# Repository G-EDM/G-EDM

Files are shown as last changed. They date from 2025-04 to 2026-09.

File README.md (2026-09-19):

</br>
</br>
</br>

```diff
 ______     _______ ______  _______
|  ____ ___ |______ |     \ |  |  |
|_____|     |______ |_____/ |  |  |      

Overview / Gateway
```                                                               

</br>
</br>

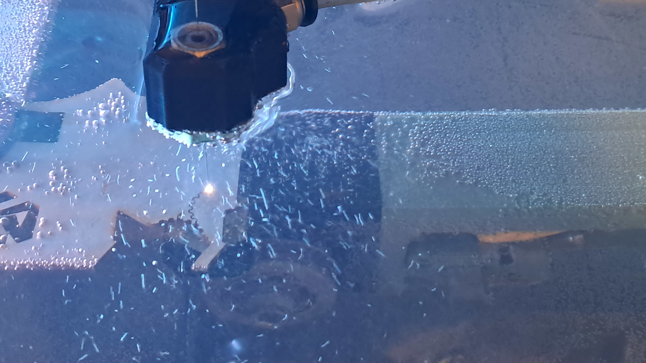
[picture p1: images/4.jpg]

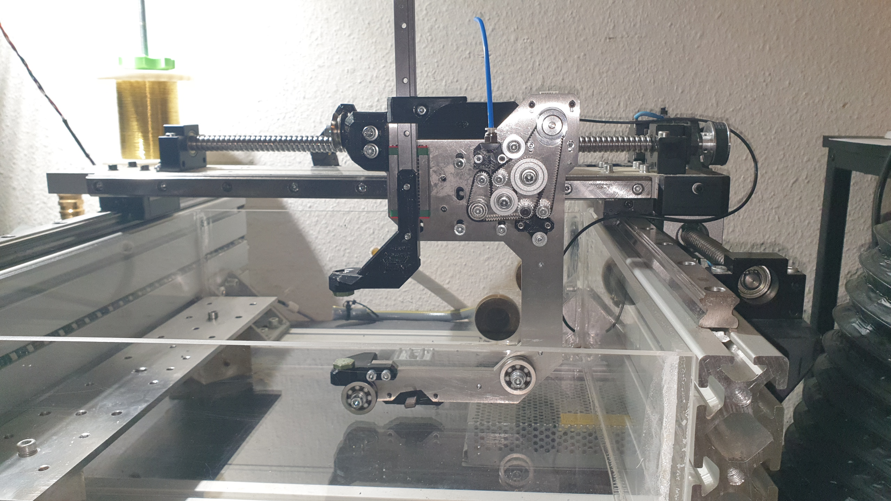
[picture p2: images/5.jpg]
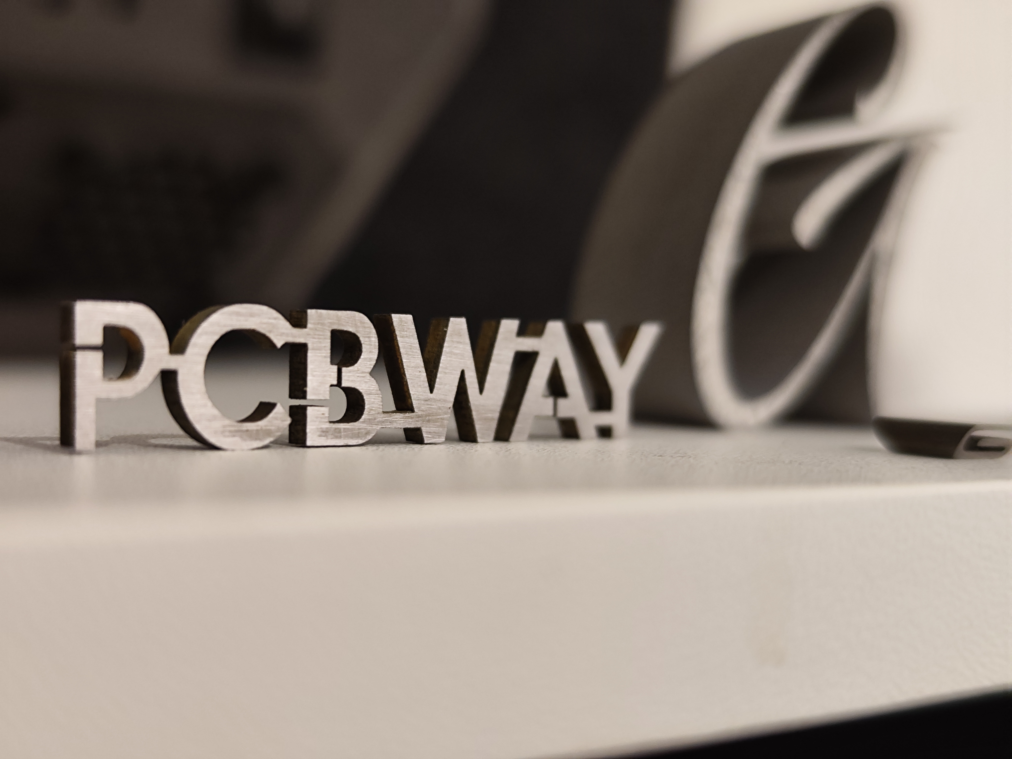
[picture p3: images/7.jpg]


</br>
</br>

# About the project

G-EDM provides Hard- and Software solution for DIY sinker and wire EDM machining targeting the hobby market while trying to keep the project affordable and low budget compatible. While this is one of the main goals there are no compromises made in regards of precision and machine rigidity.

The project evolved over time and so did the mechanical design, the electronics and the firmware.

This repo acts as a gateway to all the other repos and is a way to start the journey into the world of DIY electrical discharge machining.

There are currently two different core version of the electronics and firmware in circulation. The EVOII/III are the initial releases. The new Gapstorm components are the current and upcoming versions. 

Since the sensing circuitry has slightly changed the Gapstorm firmware is not compatible with the EVO pulseboard.

It is possible to upgrade the EVOII and III Pulseboard to match the Gapstorms. A tutorial on how to do that will follow soon. After that upgrade those baords can be used with the new firmware.

</br></br>

# Mechanics

The repo for the new gapstorm router is available here:

[Gapstorm router](https://github.com/G-EDM/gedm-gapstorm/tree/main)

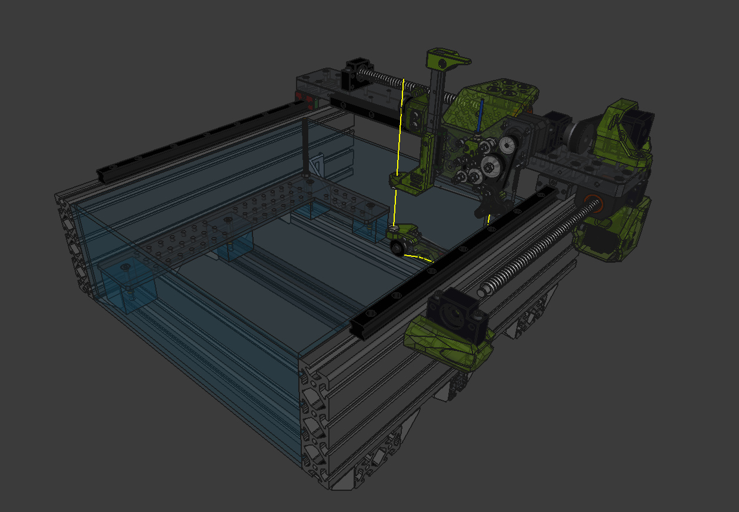
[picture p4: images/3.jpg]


</br></br>

# Electronics

The BOM for the control unit is included on this repo:

[BOM for the control unit](./control-unit-BOM.md)

Files for the PCBs are available on PCBway. To build the electronics it requires two custom PCBs. The switching PCB and the Controlboard aka Motionboard. 

The current PCBs are the Gapstorm Pulseboard and the EVOIII Motionboard.

[Gapstorm Pro Pulseboard on PCBway](https://www.pcbway.com/project/shareproject/G_EDM_Gapstorm_Pro_Pulseboard_a0db8e30.html)

[EVOIII Motionboard on PCBway](https://www.pcbway.com/project/shareproject/W532897ASC41_motionboard_evoIII_rev3_bb113e0f.html)

</br>
Tip: The Motionboard should be mounted outside of the control box that includes the Pulseboard. One way is shown on the image below using the 3D printed EVOIII Panel.
</br></br>
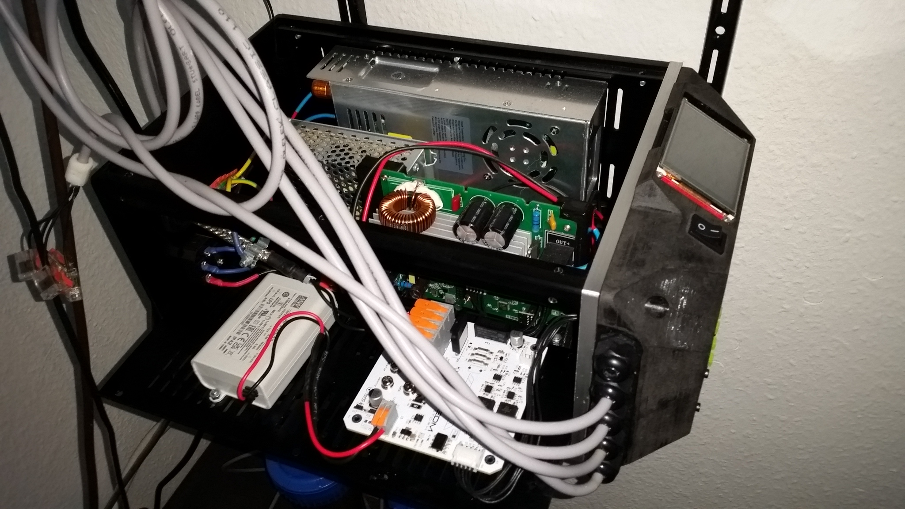
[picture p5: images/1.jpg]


More images are available here:

[Gapstorm Image gallery](https://gedm.org/photos/1/album/a655d21b876f5ba21783beb6c846ac8f)

</br></br>

# 3D printed control panel

Designed to fit a 2.8" display (see the BOM)

[EVOIII Control panel](https://github.com/G-EDM/G-EDM-EVOIII-Controlpanel)

</br></br>

# Firmware

The Repo for the Gapstorm firmware:

[Gapstorm G-RBL](https://github.com/G-EDM/G-RBLv3)

The Repo for the EVOII and EVOIII Pulseboard firmware (deprecated and not compatible with the gapstorm Pulseboard)

[EVOII/III G-RBL](https://github.com/G-EDM/G-RBL-experimental)

</br></br>

# Spool holder for P5 spools

[P5 Spool holder](https://github.com/G-EDM/spool-controller)

</br></br>

# Wiki

There is no real wiki but I posted some of the most important things on the homepage that will act like some kind of a wiki:

[G-EDM FAQ and Wiki](https://gedm.org/user/1)

</br></br>

# Contact

gedm-support@proton.me

[Join the project on Discord](https://discord.gg/vWSmpkzVrj)

[G-EDM Website](https://gedm.org)

</br>
</br>

# Donations

Bitcoin: bc1qkz8vwrd3pupewdtyg09qj9nv249vlgdy4ffhyv

Paypal: https://www.paypal.com/donate/?hosted_button_id=QP5LHGRUCXXBL

</br>   
</br>

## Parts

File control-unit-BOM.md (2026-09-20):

1x G-EDM Pulseboard

1x G-EDM Motionboard

1x ESP32 WROOM32 AZdelivery 38Pins CP2102

1x ILI9341 SPI SD TOUCH

4x TMC2209 v2 with big heatsink

1x rocker switch (ON/OFF)

JST wires of different types.

1x 12V Cooling fan (No high speed fans. Simple 120mmx20mm silent fan is ok. High Speed fans may induce noise etc.)

1x MEAN WELL APV-35-12 36W 12V 3A PSU

1x 12v 10A PSU

1x Lianshi 6A 0-80V variable voltage PSU

ONE of those (TTL version! NOT RS-485 and also not the RF version!):

    1x DPH8909 Programmable Power Supply TTL 0-96V 0-9.6A

    1x DPM8605 Programmable Power Supply TTL 0-60V 0-5A

# Cutting currents

For wire EDM current from 0.4A to 1.6A are ok to use. Depends on how good the wire feeder is and how thick the wire.
I normally settle at 1.2A or something like that. 

# Warning

EDM creates a lot of EMI noise. The motionboard with the sensitive ESP and SPI communication needs to be isolated from the 
pulsing engine. And it also should not be placed next to the sparks. A strong discharge can mess things up pretty easy.

The pulse electronics and all PSUs need to be placed inside a metal box and the motionboard needs to be outside of this box.
Best case would be to put the motionboard into a second metalbox. There are some limits about the distance between motionboard and pulseboard. The wires should be kept as short as possible and the DPH/DPM interface wire can create problems if it is too long.

# Notes

The ON/OFF switch is required! Limit switches are optional. The ON/OFF switch acts as eStop in the process too. If it is not connected or turned to OFF the process will not start and all motion is blocked.

# ESP32 note

Go for the AZdelivery boards. So far everyone who bought a cheap knockoff had issues of some kind. Inverted colors on the display was one of them. It is the heart of everything. Don't cheap out on that.

# ILI9341

There are hundreds of different version available. Not only different sizes but also different communication interface, with or without touch and with or without SD card and also different touch controllers.

The display needs to use SPI communication, XPT touch controller and provide a SD card reader.
2.8" size is nice but 2.4" works too.

It is also recommended to use the AZdelivery display.

# DPM8605 vs DPH8909

The DPH8909 will allow a higher voltage. From what I have seen it is not really needed. Cutting at 80V sounds and looks really
impressive but the surface finish is ugly. 70V is a nice working voltage. So far all showcase cuts where done with the DPM8605
at 60V and only one with the DPH8909.

The DPM8605 is still not deprecated and a valid option. It costs only half of what the DPH costs and is easily available. The DPH8909 in
the TTL version ships from china and can take two weeks to deliver.

DPM8605 has a max input voltage of around 70v. I recommend 65-70v to power it. DPH8909 can take the full max voltage of the 0-80V PSU without problems.

# About the 12V 10A PSU:

I use this exact model from Kingwen:
https://www.amazon.de/dp/B08QCNYLY8

A different one was tested but it induced noise into the motionboard and messed a little with the feedback signal.
If the cFd feedback does not produce a stable 0 reading without load the 12v PSU may be the first thing to check.
The Kingwen never made any troubles.

# About the variable voltage PSU

They don't all produce the exact same max output voltage. Some are very close to 80v and some can go up to 84v.
It is ok to use 84v if the DPH8909 is used but with the DPM8605 it needs to be set to 70v max.

Lianshi 0-80v variable voltage PSU (6A 480W):

https://www.amazon.de/dp/B0BQ33XG33

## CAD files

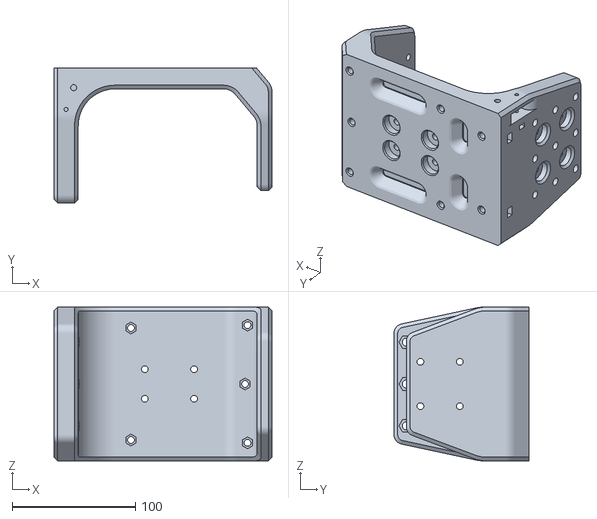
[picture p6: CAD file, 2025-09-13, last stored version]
rev2-x-slide-evoII-backport.stl
177.1 x 109.7 x 125.0

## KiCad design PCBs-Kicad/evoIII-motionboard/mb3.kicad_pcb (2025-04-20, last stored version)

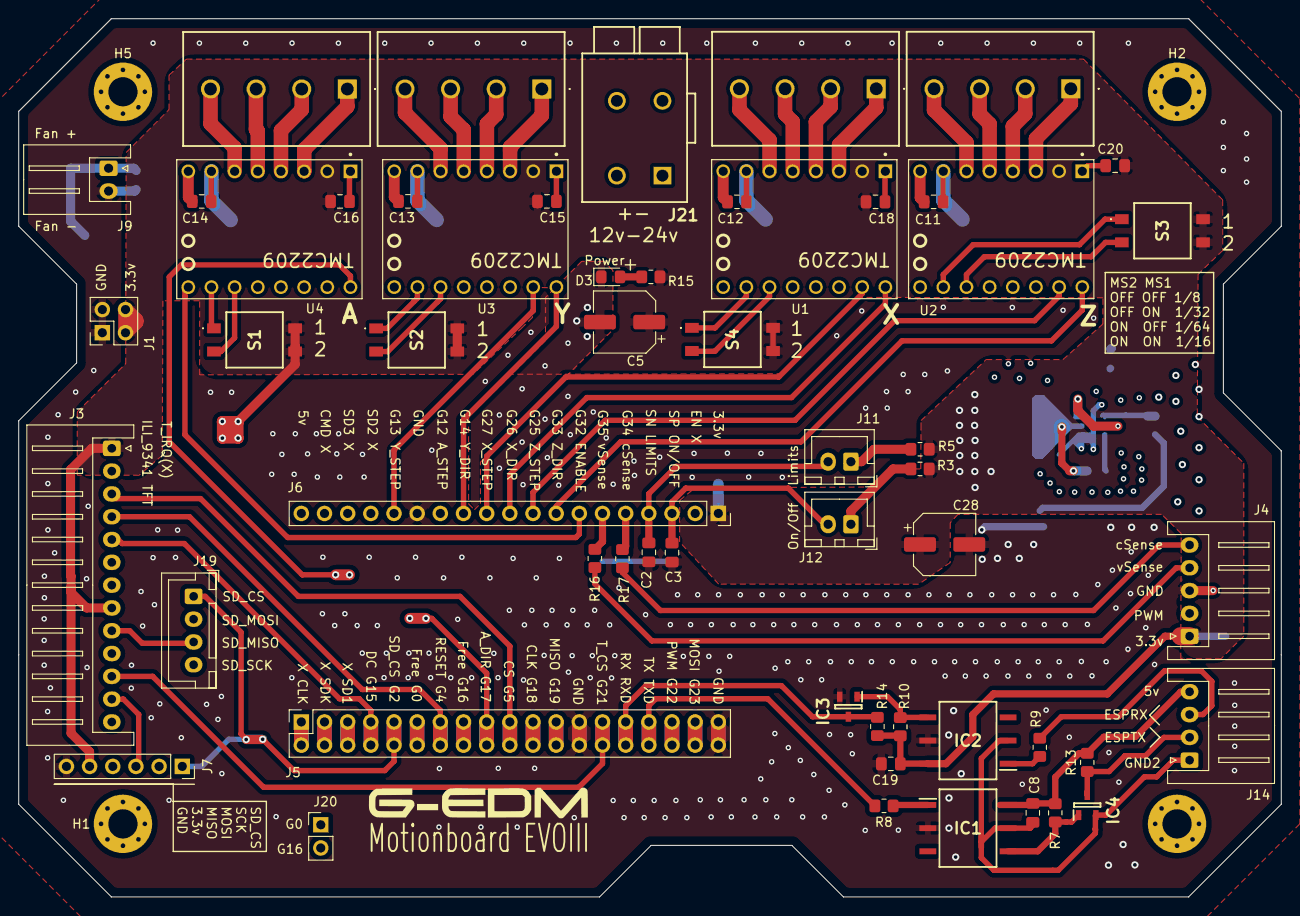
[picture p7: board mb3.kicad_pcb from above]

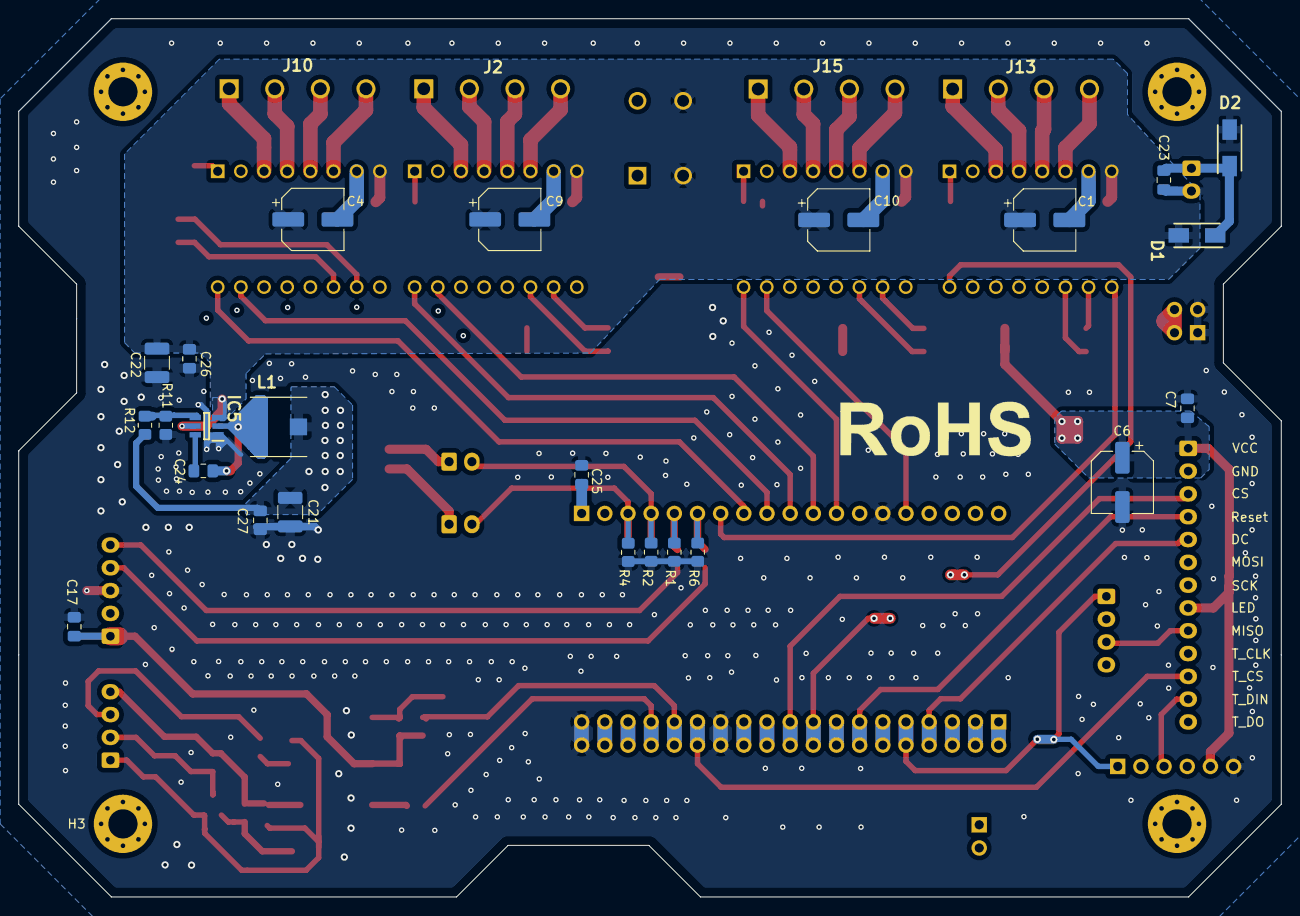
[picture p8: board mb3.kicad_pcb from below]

Board: 4 copper layers, 138.4 x 96.3 mm, 83 parts (24 on the bottom side), 73 nets.

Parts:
C1, C4, C9, C10: EEE-HA1V101XP; CP_Elec_6.3x7.7
C2, C3, C7, C8, C11, C12, C13, C14, C15, C16, C17, C18, C19, C20, C23, C24, C25, C26, C27: 08055C104K4T2A; C_0805_2012Metric_Pad1.18x1.45mm_HandSolder
C5, C6, C28: EEE-HA1C221XP; CP_Elec_6.3x7.7
C21: 22uf-16v-X7R (GRM32ER71C226KEA8K); C_1210_3225Metric_Pad1.33x2.70mm_HandSolder
C22: GRM32ER71H475KA88L; C_1210_3225Metric_Pad1.33x2.70mm_HandSolder
D1, D2: RB168L-60TFTE25; DIOM5026X220N
D3: 597-3305-607F; LED_0805_2012Metric_Pad1.15x1.40mm_HandSolder
H1, H2, H3, H5: MountingHole_Pad; MountingHole_3.2mm_M3_Pad_Via
IC1, IC2: H11L1SR2M; SOT254P916X480-6N
IC3, IC4: MMBT3904; SOT95P240X110-3N
IC5: LMR51420XFDDCR; SOT95P280X110-6N
J1: Conn_02x02_Odd_Even; PinHeader_2x02_P2.54mm_Vertical
J2, J10, J13, J15: 796689-4; 7966894
J3: B13B-XH-A(LF)(SN; JST_XH_S13B-XH-A_1x13_P2.50mm_Horizontal
J4: Conn_01x05_Socket; JST_XH_S5B-XH-A_1x05_P2.50mm_Horizontal
J5: PM254-2-19-Z-8.5; PinSocket_2x19_P2.54mm_Vertical
J6: PM254-1-19-Z-8.5; PinSocket_1x19_P2.54mm_Vertical
J7: Conn_01x06_Socket; PinSocket_1x06_P2.54mm_Vertical
J9: B2B-XH-A(LF)(SN); JST_XH_S2B-XH-A_1x02_P2.50mm_Horizontal
J11, J12: B2B-XH-A(LF)(SN); JST_XH_B2B-XH-A_1x02_P2.50mm_Vertical
J14: B4B-XH-A(LF)(SN); JST_XH_S4B-XH-A_1x04_P2.50mm_Horizontal
J19: B4B-XH-A(LF)(SN); JST_XH_B4B-XH-A_1x04_P2.50mm_Vertical
J20: DNP; PinHeader_1x02_P2.54mm_Vertical
J21: 2604-1102; 26041102
L1: 7447786008; WE-PD_6033_6050_PLASTIC_BASE54
R1, R2, R4, R6, R12, R16, R17: 560112120013; R_0805_2012Metric_Pad1.20x1.40mm_HandSolder
R3, R5: ERJ-T06J102V; R_0805_2012Metric_Pad1.20x1.40mm_HandSolder
R7, R10, R14: RCC0805470RFKEA; R_0805_2012Metric_Pad1.20x1.40mm_HandSolder
R8, R13: RCC0805330RFKEA; R_0805_2012Metric_Pad1.20x1.40mm_HandSolder
R9: MR08X4990FTL; R_0805_2012Metric_Pad1.20x1.40mm_HandSolder
R11: 560112120026; R_0805_2012Metric_Pad1.20x1.40mm_HandSolder
R15: ERJ-T06J221V; R_0805_2012Metric_Pad1.20x1.40mm_HandSolder
S1, S2, S3, S4: 2454985-2; 24549852
U1, U2, U3, U4: TMC2209; MODULE_TMC2209_SILENTSTEPSTICK

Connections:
3.3v+: C5.1, C6.1, C7.1, C15.1, C16.1, C17.1, C18.1, C19.2, C20.1, C21.2, C25.1, C27.2, C28.1, IC2.6 (VCC), J1.3, J1.4, J3.1, J3.8, J4.1, J6.1, J7.5, L1.2, R3.2, R5.2, R10.1, R12.1, R14.2, R15.1, S1.B1 (3), S1.B2 (4), S2.B1 (3), S2.B2 (4), S3.B1 (3), S3.B2 (4), S4.B1 (3), S4.B2 (4), U1.2 (VIO), U2.2 (VIO), U3.2 (VIO), U4.2 (VIO)
12v+: C1.1, C4.1, C9.1, C10.1, C11.1, C12.1, C13.1, C14.1, C22.2, C26.2, D1.2 (A), IC5.3 (VIN), IC5.5 (EN), J21.3 (2.1), J21.4 (2.2), U1.8 (VM), U2.8 (VM), U3.8 (VM), U4.8 (VM)
CLK: J3.7, J3.10, J5.21, J5.22, J7.2, J19.4
CS: J3.3, J5.19, J5.20
DC: J3.5, J5.7, J5.8
DPMRXB: IC4.3 (COLLECTOR), J14.2, R13.1
DPMTXB: J14.3, R9.1
GND: C1.2, C2.2, C3.2, C4.2, C5.2, C6.2, C7.2, C9.2, C10.2, C11.2, C12.2, C13.2, C14.2, C15.2, C16.2, C17.2, C18.2, C19.1, C20.2, C21.1, C22.1, C23.2, C25.2, C26.1, C27.1, C28.2, D2.2 (A), D3.1 (K), IC1.2 (CATHODE), IC2.5 (GND), IC3.2 (EMITTER), IC5.1 (GND), J1.1, J1.2, J3.2, J4.3, J5.25, J5.26, J5.37, J5.38, J6.14, J7.6, J9.2, J21.1 (1.1), J21.2 (1.2), R1.2, R2.2, R4.2, R6.2, R11.2, U1.1 (GND), U1.7 (GND), U2.1 (GND), U2.7 (GND), U3.1 (GND), U3.7 (GND), U4.1 (GND), U4.7 (GND)
GND5v: C8.1, IC1.5 (GND), IC2.2 (CATHODE), IC4.2 (EMITTER), J14.1
GPIO16: J5.15, J5.16, J20.2
Limit39: C2.1, J6.4, J11.2, R2.1
MOSI: J3.6, J3.12, J5.35, J5.36, J7.3, J19.2
Miso: J3.9, J3.13, J5.23, J5.24, J7.4, J19.3
unnamed: C23.1, D1.1 (K), D2.1 (K), J9.1
unnamed: D3.2 (A), R15.2
unnamed: IC1.1 (ANODE), R8.2
unnamed: IC1.4 (VO), IC4.1 (BASE), R7.2
unnamed: IC2.1 (ANODE), R9.2
unnamed: IC2.4 (VO), IC3.1 (BASE), R10.2
unnamed: C24.1, IC5.6 (CB)
unnamed: IC5.4 (FB), R11.1, R12.2
unnamed: C24.2, IC5.2 (SW), L1.1
unnamed: J4.4, R16.1
unnamed: J4.5, R17.1
unnamed: J5.1, J5.2
unnamed: J5.3, J5.4
unnamed: J5.5, J5.6
unnamed: J11.1, R5.1
unnamed: J12.1, R3.1
unnamed: J2.2, U1.4 (M1A)
unnamed: J2.1, U1.3 (M1B)
unnamed: J2.3, U1.5 (M2A)
unnamed: J2.4, U1.6 (M2B)
unnamed: J10.2, U2.4 (M1A)
unnamed: J10.1, U2.3 (M1B)
unnamed: J10.3, U2.5 (M2A)
unnamed: J10.4, U2.6 (M2B)
unnamed: J15.2, U3.4 (M1A)
unnamed: J15.1, U3.3 (M1B)
unnamed: J15.3, U3.5 (M2A)
unnamed: J15.4, U3.6 (M2B)
unnamed: J13.2, U4.4 (M1A)
unnamed: J13.1, U4.3 (M1B)
unnamed: J13.3, U4.5 (M2A)
unnamed: J13.4, U4.6 (M2B)
PWM: J4.2, J5.33, J5.34
RX(IO3): IC3.3 (COLLECTOR), J5.29, J5.30, R14.1
SD_CS: J5.9, J5.10, J7.1, J19.1
Start36: C3.1, J6.3, J12.2, R4.1
TX(IO1): J5.31, J5.32, R8.1
T_CS: J3.11, J5.27, J5.28
VCCB: C8.2, IC1.6 (VCC), J14.4, R7.1, R13.2
adir17: J5.17, J5.18, U4.9 (DIR)
ams1: S1.A1 (1), U4.15 (MS1)
ams2: S1.A2 (2), U4.14 (MS2)
astep12: J6.13, U4.10 (STEP)
enable-all: J6.7, U1.16 (~EN), U2.16 (~EN), U3.16 (~EN), U4.16 (~EN)
gpio0: J5.11, J5.12, J20.1
input35: J6.6, R6.1, R16.2
reset: J3.4, J5.13, J5.14
vSense34: J6.5, R1.1, R17.2
xdir: J6.10, U1.9 (DIR)
xms1: S4.A1 (1), U1.15 (MS1)
xms2: S4.A2 (2), U1.14 (MS2)
xstep: J6.11, U1.10 (STEP)
ydir: J6.12, U3.9 (DIR)
yms1: S2.A1 (1), U3.15 (MS1)
yms2: S2.A2 (2), U3.14 (MS2)
ystep: J6.15, U3.10 (STEP)
zdir: J6.8, U2.9 (DIR)
zms1: S3.A1 (1), U2.15 (MS1)
zms2: S3.A2 (2), U2.14 (MS2)
zstep: J6.9, U2.10 (STEP)

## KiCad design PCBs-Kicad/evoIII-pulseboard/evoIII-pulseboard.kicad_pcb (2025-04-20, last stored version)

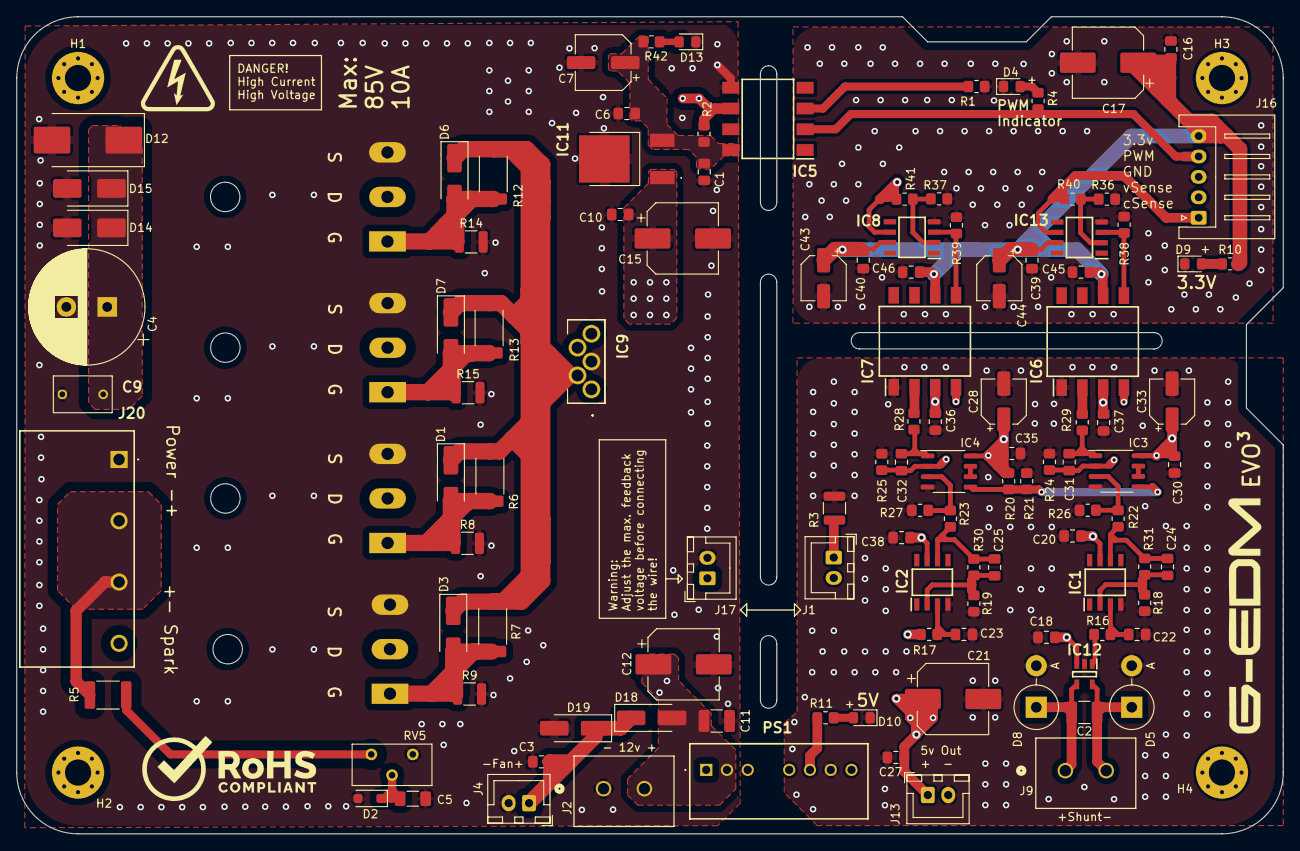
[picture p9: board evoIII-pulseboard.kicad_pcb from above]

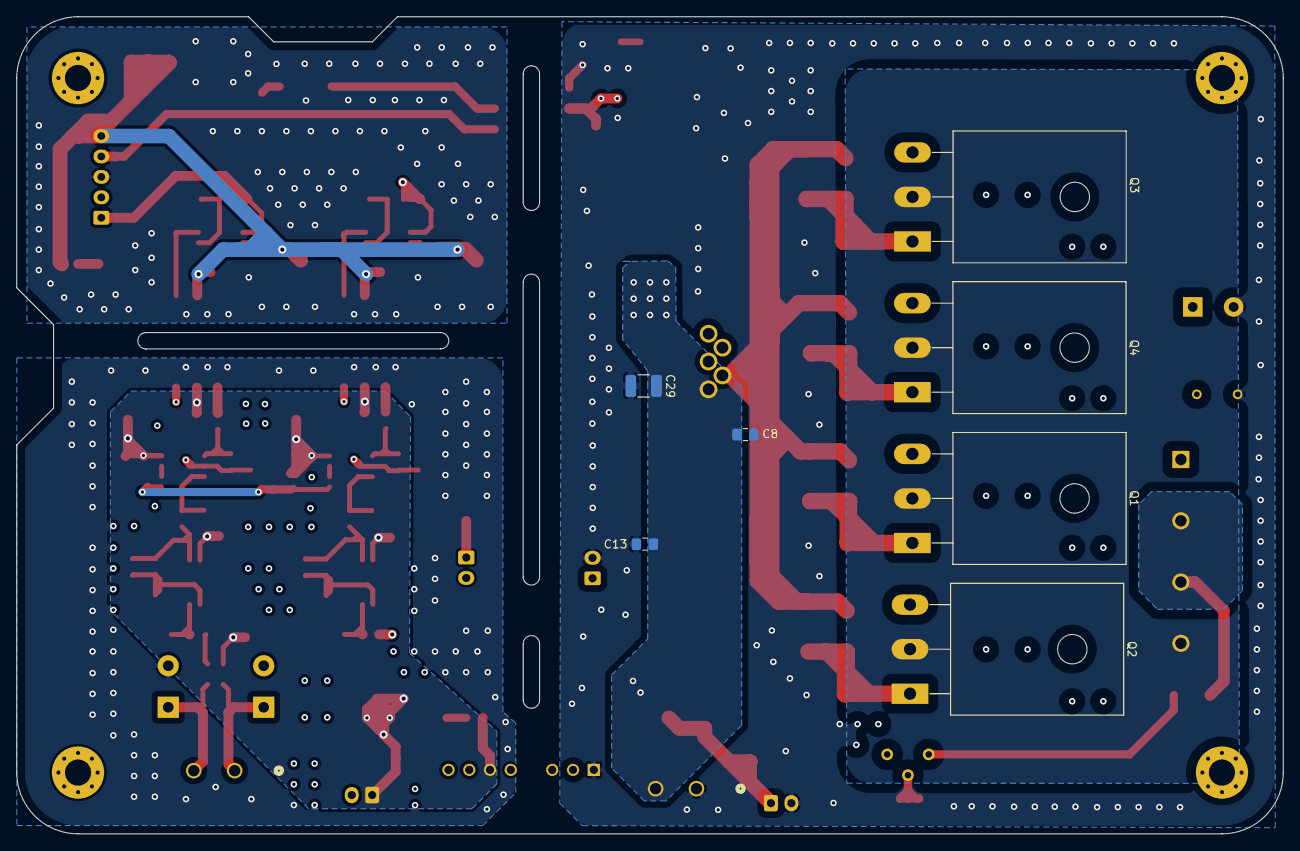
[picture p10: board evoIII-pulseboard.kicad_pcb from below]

Board: 4 copper layers, 155.0 x 100.0 mm, 124 parts (7 on the bottom side), 52 nets.

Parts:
C1, C3, C6, C8, C10, C13, C16, C18, C20, C27, C30, C35, C36, C37, C38, C39, C40, C45, C46: 08055C104K4T2A; C_0805_2012Metric_Pad1.18x1.45mm_HandSolder
C2: 12107A101JAT2A; C_1210_3225Metric_Pad1.33x2.70mm_HandSolder
C4: DNP; CP_Radial_D14.0mm_P5.00mm
C5: DNP; C_1206_3216Metric_Pad1.33x1.80mm_HandSolder
C7: EEE-HAC221XAP; CP_Elec_6.3x7.7
C9: FKP2F004701D00JSSD; FKP2G011001D00KI00
C11, C29: GRM32RR71H105KA01K; C_1210_3225Metric_Pad1.33x2.70mm_HandSolder
C12, C15, C17, C21: EEE-HAV221UAP; CP_Elec_8x10.5
C22, C23, C31, C32: C0805C101J5RACTU; C_0805_2012Metric_Pad1.18x1.45mm_HandSolder
C24, C25: DNP; C_0805_2012Metric_Pad1.18x1.45mm_HandSolder
C28, C33, C43, C44: AVS476M16C12T-F; CP_Elec_5x5.4
D1, D3, D6, D7, D18, D19: B360A-E3/61T; D_SMA_Handsoldering
D2: DNP; D_SOD-123F
D4: APT2012LVBC/D; LED_0805_2012Metric_Pad1.15x1.40mm_HandSolder
D5, D8: 1N5378B; D_DO-201_P5.08mm_Vertical_AnodeUp
D9, D10, D13: SM0805UGC; LED_0805_2012Metric_Pad1.15x1.40mm_HandSolder
D12: MB520_R1_00001; D_SMC_Handsoldering
D14, D15: SMBJ5378B-TP; D_SMB_Handsoldering
H1, H2, H4: MountingHole; MountingHole_3.2mm_M3_Pad_Via
H3: MountingHole_Pad; MountingHole_3.2mm_M3_Pad_Via
IC1, IC2, IC8, IC13: OPA350UA; SOIC127P600X175-8N
IC3, IC4: LM358F-GE2; SOP-8_3.9x4.9mm_P1.27mm
IC5: 6N137S; SOP254P1016X460-8N
IC6, IC7: HCNR201-500E; SOP254P1230X400-8N
IC9: IXDI609CI
IC11: MC7805CDTRKG; MJD1221G
IC12: INA293B3; SOT95P280X145-5N
J1, J13, J17: B2B-XH-A(LF)(SN); JST_XH_B2B-XH-A_1x02_P2.50mm_Vertical
J2: 1776138-2 and 796641-2; CONN2_796643-2_TEC
J4: S2B-XH-A(LF)(SN); JST_XH_B2B-XH-A_1x02_P2.50mm_Vertical
J9: 1776138-2, 796641-2; CONN2_796643-2_TEC
J16: S5B-XH-A(LF)(SN); JST_XH_S5B-XH-A_1x05_P2.50mm_Horizontal
J20: 8000078309, 8000078355; 8000078309
PS1: RS3K-2405SZ/H3; RS3K2405SZH3
Q1, Q2, Q3, Q4: IRFP260NPBF; TO-247-3_Horizontal_TabUp
R1, R28, R29: 560112120015; R_0805_2012Metric_Pad1.20x1.40mm_HandSolder
R2, R20, R21, R22, R23: 560112120004; R_0805_2012Metric_Pad1.20x1.40mm_HandSolder
R3: CRCW12101K00JNEAIF; R_1210_3225Metric
R4, R10: ERJ-T06J221V; R_0805_2012Metric_Pad1.20x1.40mm_HandSolder
R5: ERJ-U12F1001U; R_1812_4532Metric_Pad1.30x3.40mm_HandSolder
R6, R7, R12, R13: RC2512JK-7W4R7L; R_2512_6332Metric_Pad1.40x3.35mm_HandSolder
R8, R9, R14, R15: RK73B2ETTD104J; R_1210_3225Metric
R11, R42: RK73B2ATTD561J; R_0805_2012Metric_Pad1.20x1.40mm_HandSolder
R16, R17, R18, R19: RCC08051K00FKEA; R_0805_2012Metric_Pad1.20x1.40mm_HandSolder
R24, R25, R38, R39: 560112120013; R_0805_2012Metric_Pad1.20x1.40mm_HandSolder
R26, R27: RCC08054K70FKEA; R_0805_2012Metric_Pad1.20x1.40mm_HandSolder
R30, R31: RCC08050000Z0EA; R_0805_2012Metric_Pad1.20x1.40mm_HandSolder
R36, R37, R40, R41: RK73H2ARTTD2002F; R_0805_2012Metric_Pad1.20x1.40mm_HandSolder
RV5: 3296Y-1-103LF; Potentiometer_Bourns_3296Y_Vertical

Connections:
2.5V: IC3.5 (2IN+), IC4.5 (2IN+), R20.2, R21.1
5v: C1.1, C6.1, C7.1, IC5.8 (VCC), IC11.3 (OUTPUT), R2.1, R42.2
5v-optoout: IC5.6 (VO), IC9.4 (IN), R2.2
12vpower: C8.1, C10.1, C11.1, C12.1, C13.1, C15.1, C29.1, D18.2 (A), IC9.1 (VCC), IC11.1 (INPUT), J2.2, PS1.2 (+VIN)
+48V: C4.1, C9.2, D12.1 (K), D14.1 (K), D15.1 (K), J20.2, J20.3, R5.1
ESP3.3v: C16.1, C17.1, C39.1, C40.1, C43.1, C44.1, C45.1, C46.1, IC6.6 (PD2_CATHODE), IC7.6 (PD2_CATHODE), IC8.7 (V+), IC13.7 (V+), J16.5, R10.2
GND1: C16.2, C17.2, C39.2, C40.2, C43.2, C44.2, C45.2, C46.2, D4.1 (K), D9.1 (K), IC8.4 (V-), IC13.4 (V-), J16.3, R1.2, R36.1, R37.1, R38.1, R39.1
GND2: C1.2, C3.1, C4.2, C5.2, C6.2, C7.2, C8.2, C9.1, C10.2, C11.2, C12.2, C13.2, C15.2, C29.2, D2.2 (A), D12.2 (A), D13.1 (K), D14.2 (A), D15.2 (A), D19.2 (A), IC5.5 (GND), IC9.3 (GND), IC11.2 (GROUND), J2.1, J4.2, J17.2, J20.1, PS1.1 (-VIN), Q1.3 (S), Q2.3 (S), Q3.3 (S), Q4.3 (S), R8.2, R9.2, R14.2, R15.2, RV5.1
GND3: C18.1, C20.2, C21.2, C22.2, C23.2, C27.2, C28.2, C30.2, C33.2, C35.1, C36.1, C37.1, C38.1, D5.2 (A), D8.2 (A), D10.1 (K), IC1.4 (V-), IC2.4 (V-), IC3.4 (GND), IC4.4 (GND), IC6.1 (LED_CATHODE), IC7.1 (LED_CATHODE), IC12.2 (GND), J13.2, PS1.7 (-VOUT), R3.1, R18.2, R19.2, R21.2, R24.1, R25.1, R26.2, R27.2
Gatedriverout: D1.1 (K), D3.1 (K), D6.1 (K), D7.1 (K), IC9.2 (~OUT), R6.2, R7.2, R12.2, R13.2
ISO+5v: C18.2, C20.1, C21.1, C27.1, C28.1, C30.1, C33.1, C35.2, C36.2, C37.2, C38.2, IC1.7 (V+), IC2.7 (V+), IC3.8 (VCC), IC4.8 (VCC), IC6.3 (PD1_CATHODE), IC7.3 (PD1_CATHODE), IC12.3 (VS), J13.1, PS1.6 (+VOUT), R11.2, R20.1
Isolated-csense-out: IC13.6 (OUTPUT), J16.1, R40.2
Isolated-vsense-out: IC8.6 (OUTPUT), J16.2, R41.2
unnamed: D1.2 (A), Q1.1 (G), R6.1, R8.1
unnamed: C5.1, D2.1 (K), J17.1, RV5.2
unnamed: D3.2 (A), Q2.1 (G), R7.1, R9.1
unnamed: D4.2 (A), R4.1
unnamed: C2.1, D5.1 (K), IC12.5 (IN-), J9.2
unnamed: D6.2 (A), Q3.1 (G), R12.1, R14.1
unnamed: D7.2 (A), Q4.1 (G), R13.1, R15.1
unnamed: C2.2, D8.1 (K), IC12.4 (IN+), J9.1
unnamed: D9.2 (A), R10.1
unnamed: D10.2 (A), R11.1
unnamed: D13.2 (A), R42.1
unnamed: C3.2, D18.1 (K), D19.1 (K), J4.1
unnamed: C22.1, IC1.3 (+IN), R16.2
unnamed: C24.2, IC1.2 (-IN), R18.1, R31.2
unnamed: C24.1, IC1.6 (OUTPUT), R22.2, R31.1
unnamed: C23.1, IC2.3 (+IN), R17.2
unnamed: C25.2, IC2.2 (-IN), R19.1, R30.2
unnamed: C25.1, IC2.6 (OUTPUT), R23.2, R30.1
unnamed: IC3.3 (1IN+), R22.1, R26.1
unnamed: C31.1, IC3.2 (1IN-), IC6.4 (PD1_ANODE), R24.2
unnamed: C31.2, IC3.1 (1OUT), R29.2
unnamed: IC3.6 (2IN-), IC3.7 (2OUT)
unnamed: IC4.3 (1IN+), R23.1, R27.1
unnamed: C32.1, IC4.2 (1IN-), IC7.4 (PD1_ANODE), R25.2
unnamed: C32.2, IC4.1 (1OUT), R28.2
unnamed: IC4.6 (2IN-), IC4.7 (2OUT)
unnamed: IC5.3 (CATHODE), R1.1
unnamed: IC6.2 (LED_ANODE), R29.1
unnamed: IC7.2 (LED_ANODE), R28.1
unnamed: IC7.5 (PD2_ANODE), IC8.3 (+IN), R39.2
unnamed: IC8.2 (-IN), R37.2, R41.1
unnamed: IC12.1 (OUT), R16.1
unnamed: IC6.5 (PD2_ANODE), IC13.3 (+IN), R38.2
unnamed: IC13.2 (-IN), R36.2, R40.1
unnamed: J1.1, R3.2
unnamed: J1.2, R17.1
unnamed: R5.2, RV5.3
pwm-in: IC5.2 (ANODE), J16.4, R4.2
spark-minus-to-drain: J20.4, Q1.2 (D), Q2.2 (D), Q3.2 (D), Q4.2 (D)

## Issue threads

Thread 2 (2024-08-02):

pulse generator

kzali, 2024-08-02:
Is this project abandoned? and I cannot find the schematics of the pulse generator.  I am new here so pardon me if I am missing something

G-EDM, 2024-08-02:
If you check the youtube channel and the community section you can get some fresh updates on the projects current status. There is heavy development going on. I just ordered new PCB prototypes and spend days soldering stuff.

https://www.youtube.com/@G-EDM/community

The schematics itself is not yet released. The new boards need approval first.  You can contact me via email if you're interested in the files. goblin-dev@proton.me

Once the new boards are tested and working I may upload some files.

kzali, 2024-08-02:
Thanks for this quick respone.  Great work.  I will wait for your upload.  I dont have a job right now but will donate as soon as I am able to

G-EDM, 2024-08-02:
Good to hear. I'm happy about every cup of free coffee. Can't tell yet how long it takes but things move as fast as possible.

G-EDM, 2024-08-13:
https://github.com/G-EDM/GEDM-EVO2-CNC/tree/main/files/schematics-and-gerbers

Closed 2024-08-02.
